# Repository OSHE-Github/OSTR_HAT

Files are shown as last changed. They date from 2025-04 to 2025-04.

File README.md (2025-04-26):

# PCB design for the Open Source Thunniform Robot Project

### Check us out and find more documentation at oshe.io!

### This is the repository for the versitile Raspberry Pi HAT that was developed for the OSTR project in the Open Source Hardware Enterprise at Michigan Tech. This PCB has the following capabilities:
* Can drive two bidirectional 12 V DC motors or four unidirectional 12 V DC motors
* Can control up to two 5 V servos and read from the feedback potentiometer if it's broken out of the servo. These headers can also be used as 5 V ADC inputs
* Has three 3.3 V ADC headers with 3.3 V and GND available. Can be used to read from a potentiometer.
* Two 3.3 V PWM headers with GND and 5 V
* Two GPIO headers with GND and 3.3 V
* Two 3.3 V I2C headers, one is designed/located to be used with the MPU6050 IMU
* Screw terminal 1-wire port designed for a 1-wire based temperature sensor
* Wide input voltage range of 7 V - 30 V using a DFR1015 buck converter
* Capable of monitoring the input voltage. Useful for running off of a battery
* Capable of measuring the output current of both motor drivers (uses two DRV8874 motor drivers)
* Two audio amplifiers designed to be used with custom built piezo electric disk based transducers

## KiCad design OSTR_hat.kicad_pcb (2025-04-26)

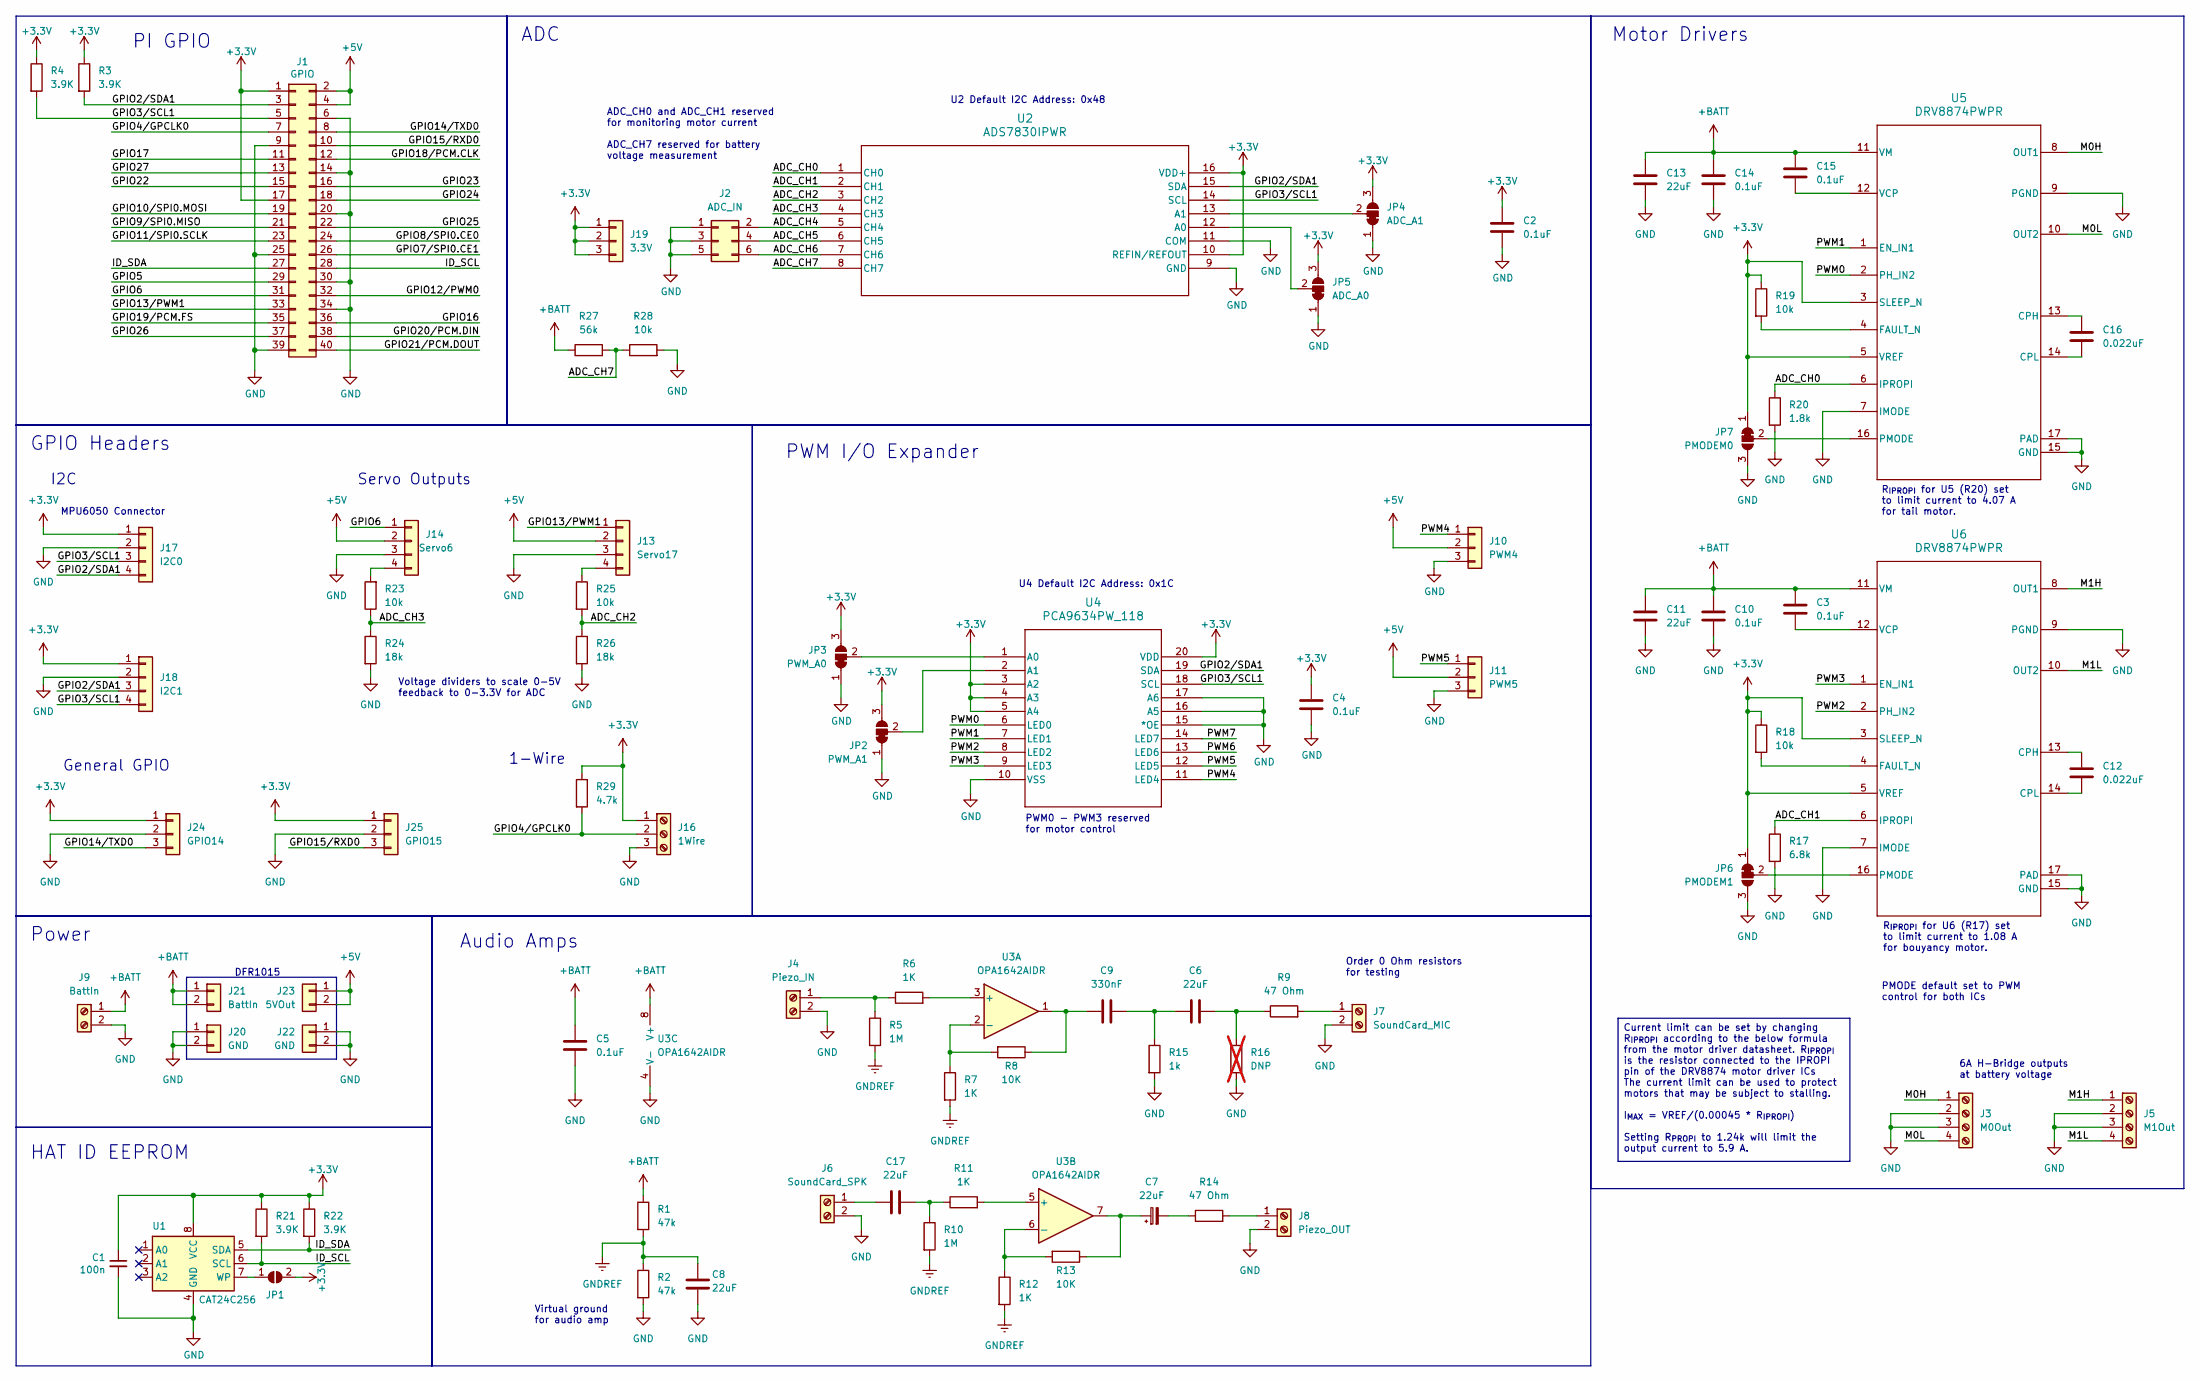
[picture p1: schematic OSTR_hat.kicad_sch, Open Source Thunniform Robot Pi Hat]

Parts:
C1: 100n; C_0603_1608Metric
C2, C4, C5: 0.1uF; C_0603_1608Metric
C3, C15: 0.1uF; C_0603_1608Metric; Part Number C1206C104K5RACTU
C6, C7, C8, C11, C13, C17: 22uF; C_0603_1608Metric
C9: 330nF; C_0603_1608Metric
C10, C14: 0.1uF; C_0603_1608Metric; Part Number GRM155R71C104KA88J
C12, C16: 0.022uF; C_0603_1608Metric; Part Nember C0805C223K5RACTU
J1: GPIO; PinSocket_2x20_P2.54mm_Vertical
J2: ADC_IN; PinHeader_2x03_P2.54mm_Vertical
J3: M0Out; TerminalBlock_Phoenix_MPT-0,5-4-2.54_1x04_P2.54mm_Horizontal
J4: Piezo_IN; TerminalBlock_Phoenix_MPT-0,5-2-2.54_1x02_P2.54mm_Horizontal
J5: M1Out; TerminalBlock_Phoenix_MPT-0,5-4-2.54_1x04_P2.54mm_Horizontal
J6: SoundCard_SPK; TerminalBlock_Phoenix_MPT-0,5-2-2.54_1x02_P2.54mm_Horizontal
J7: SoundCard_MIC; TerminalBlock_Phoenix_MPT-0,5-2-2.54_1x02_P2.54mm_Horizontal
J8: Piezo_OUT; TerminalBlock_Phoenix_MPT-0,5-2-2.54_1x02_P2.54mm_Horizontal
J9: BattIn; TerminalBlock_Phoenix_MKDS-1,5-2-5.08_1x02_P5.08mm_Horizont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
J10: PWM4; PinHeader_1x03_P2.54mm_Vertical
J11: PWM5; PinHeader_1x03_P2.54mm_Vertical
J13: Servo17; PinHeader_1x04_P2.54mm_Vertical
J14: Servo6; PinHeader_1x04_P2.54mm_Vertical
J16: 1Wire; TerminalBlock_Phoenix_MPT-0,5-3-2.54_1x03_P2.54mm_Horizontal
J17: I2C0; PinHeader_1x04_P2.54mm_Vertical
J18: I2C1; PinHeader_1x04_P2.54mm_Vertical
J19: 3.3V; PinHeader_1x03_P2.54mm_Vertical
J20, J22: GND; PinHeader_1x02_P2.54mm_Vertical
J21: BattIn; PinHeader_1x02_P2.54mm_Vertical
J23: 5VOut; PinHeader_1x02_P2.54mm_Vertical
J24: GPIO14; PinHeader_1x03_P2.54mm_Vertical
J25: GPIO15; PinHeader_1x03_P2.54mm_Vertical
JP1: ID_WP; SolderJumper-2_P1.3mm_Open_Pad1.0x1.5mm
JP2: PWM_A1; SolderJumper-3_P1.3mm_Bridged12_Pad1.0x1.5mm
JP3: PWM_A0; SolderJumper-3_P1.3mm_Bridged12_Pad1.0x1.5mm
JP4: ADC_A1; SolderJumper-3_P1.3mm_Bridged12_Pad1.0x1.5mm
JP5: ADC_A0; SolderJumper-3_P1.3mm_Bridged12_Pad1.0x1.5mm
JP6: PMODEM1; SolderJumper-3_P1.3mm_Bridged12_Pad1.0x1.5mm
JP7: PMODEM0; SolderJumper-3_P1.3mm_Bridged12_Pad1.0x1.5mm
R1, R2: 47k; R_0603_1608Metric
R3, R4, R21, R22: 3.9K; R_0603_1608Metric
R5, R10: 1M; R_0603_1608Metric
R6, R7, R11, R12: 1K; R_0603_1608Metric
R8, R13: 10K; R_0603_1608Metric
R9, R14: 47 Ohm; R_0603_1608Metric
R15: 1k; R_0603_1608Metric
R16: DNP; R_0603_1608Metric; not fitted
R17: 6.8k; R_0603_1608Metric
R18, R19, R23, R25, R28: 10k; R_0603_1608Metric
R20: 1.8k; R_0603_1608Metric
R24, R26: 18k; R_0603_1608Metric
R27: 56k; R_0603_1608Metric
R29: 4.7k; R_0603_1608Metric
U1: CAT24C256; SOIC127P600X175-8N
U2: ADS7830IPWR; TSSOP-16_4.4x5mm_P0.65mm
U3: OPA1642AIDR; SOIC-8_3.9x4.9mm_P1.27mm
U4: PCA9634PW_118; TSSOP-20_4.4x6.5mm_P0.65mm
U5, U6: DRV8874PWPR; PWP0016J_M

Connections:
+3.3V: C1.1, C2.1, C4.1, J1.1, J1.17, J16.1, J17.1, J18.1, J19.1, J19.2, J19.3, J24.1, J25.1, JP1.2 (B), JP2.3 (B), JP3.3 (B), JP4.3 (B), JP5.3 (B), JP6.1 (A), JP7.1 (A), R3.1, R4.1, R18.1, R19.1, R21.1, R22.1, R29.1, U1.8 (VCC), U2.10 (REFIN/REFOUT), U2.16 (VDD+), U4.3 (A2), U4.4 (A3), U4.5 (A4), U4.20 (VDD), U5.3 (SLEEP_N), U5.5 (VREF), U6.3 (SLEEP_N), U6.5 (VREF)
+5V: J1.2, J1.4, J10.2, J11.2, J13.2, J14.2, J23.1, J23.2
+BATT: C3.1, C5.1, C10.1, C11.1, C13.1, C14.1, C15.1, J9.1, J21.1, J21.2, R1.1, R27.1, U3.8 (V+), U5.11 (VM), U6.11 (VM)
/ADC_CH0: R20.1, U2.1 (CH0), U5.6 (IPROPI)
/ADC_CH1: R17.1, U2.2 (CH1), U6.6 (IPROPI)
/ADC_CH2: R25.2, R26.1, U2.3 (CH2)
/ADC_CH3: R23.1, R24.1, U2.4 (CH3)
/ADC_CH4: J2.2, U2.5 (CH4)
/ADC_CH5: J2.4, U2.6 (CH5)
/ADC_CH6: J2.6, U2.7 (CH6)
/ADC_CH7: R27.2, R28.1, U2.8 (CH7)
/GPIO2/SDA1: J1.3, J17.4, J18.3, R3.2, U2.15 (SDA), U4.19 (SDA)
/GPIO3/SCL1: J1.5, J17.3, J18.4, R4.2, U2.14 (SCL), U4.18 (SCL)
/GPIO4/GPCLK0: J1.7, J16.2, R29.2
/GPIO5: J1.29
/GPIO6: J1.31, J14.1
/GPIO7/SPI0.CE1: J1.26
/GPIO8/SPI0.CE0: J1.24
/GPIO9/SPI0.MISO: J1.21
/GPIO10/SPI0.MOSI: J1.19
/GPIO11/SPI0.SCLK: J1.23
/GPIO12/PWM0: J1.32
/GPIO13/PWM1: J1.33, J13.1
/GPIO14/TXD0: J1.8, J24.3
/GPIO15/RXD0: J1.10, J25.3
/GPIO16: J1.36
/GPIO17: J1.11
/GPIO18/PCM.CLK: J1.12
/GPIO19/PCM.FS: J1.35
/GPIO20/PCM.DIN: J1.38
/GPIO21/PCM.DOUT: J1.40
/GPIO22: J1.15
/GPIO23: J1.16
/GPIO24: J1.18
/GPIO25: J1.22
/GPIO26: J1.37
/GPIO27: J1.13
/ID_SCL: J1.28, R21.2, U1.6 (SCL)
/ID_SDA: J1.27, R22.2, U1.5 (SDA)
/M0H: J3.1, U5.8 (OUT1)
/M0L: J3.4, U5.10 (OUT2)
/M1H: J5.1, U6.8 (OUT1)
/M1L: J5.4, U6.10 (OUT2)
/PWM0: U4.6 (LED0), U5.2 (PH_IN2)
/PWM1: U4.7 (LED1), U5.1 (EN_IN1)
/PWM2: U4.8 (LED2), U6.2 (PH_IN2)
/PWM3: U4.9 (LED3), U6.1 (EN_IN1)
/PWM4: J10.1, U4.11 (LED4)
/PWM5: J11.1, U4.12 (LED5)
/PWM6: U4.13 (LED6)
/PWM7: U4.14 (LED7)
GND: C1.2, C2.2, C4.2, C5.2, C8.2, C10.2, C11.2, C13.2, C14.2, J1.6, J1.9, J1.14, J1.20, J1.25, J1.30, J1.34, J1.39, J2.1, J2.3, J2.5, J3.2, J3.3, J4.2, J5.2, J5.3, J6.2, J7.2, J8.2, J9.2, J10.3, J11.3, J13.3, J14.3, J16.3, J17.2, J18.2, J20.1, J20.2, J22.1, J22.2, J24.2, J25.2, JP2.1 (A), JP3.1 (A), JP4.1 (A), JP5.1 (A), JP6.3 (B), JP7.3 (B), R2.2, R15.2, R16.2, R17.2, R20.2, R24.2, R26.2, R28.2, U1.4 (GND), U2.9 (GND), U2.11 (COM), U3.4 (V-), U4.10 (VSS), U4.15 (*OE), U4.16 (A5), U4.17 (A6), U5.7 (IMODE), U5.9 (PGND), U5.15 (GND), U5.17 (PAD), U6.7 (IMODE), U6.9 (PGND), U6.15 (GND), U6.17 (PAD)
GNDREF: C8.1, R1.2, R2.1, R5.2, R7.2, R10.2, R12.2
unnamed: C6.1, C9.2, R15.1
unnamed: C6.2, R9.1, R16.1
unnamed: C7.1, R13.1, U3.7
unnamed: C7.2, R14.1
unnamed: C9.1, R8.1, U3.1
unnamed: C17.2, R10.1, R11.1
unnamed: J4.1, R5.1, R6.1
unnamed: C17.1, J6.1
unnamed: J7.1, R9.2
unnamed: J8.1, R14.2
unnamed: J13.4, R25.1
unnamed: J14.4, R23.2
unnamed: JP1.1 (A), U1.7 (WP)
unnamed: JP2.2 (C), U4.2 (A1)
unnamed: JP3.2 (C), U4.1 (A0)
unnamed: JP4.2 (C), U2.13 (A1)
unnamed: JP5.2 (C), U2.12 (A0)
unnamed: JP6.2 (C), U6.16 (PMODE)
unnamed: JP7.2 (C), U5.16 (PMODE)
unnamed: R6.2, U3.3 (+)
unnamed: R7.1, R8.2, U3.2 (-)
unnamed: R11.2, U3.5 (+)
unnamed: R12.1, R13.2, U3.6 (-)
unnamed: C16.1, U5.13 (CPH)
unnamed: C16.2, U5.14 (CPL)
unnamed: R19.2, U5.4 (FAULT_N)
unnamed: C15.2, U5.12 (VCP)
unnamed: C12.1, U6.13 (CPH)
unnamed: C12.2, U6.14 (CPL)
unnamed: R18.2, U6.4 (FAULT_N)
unnamed: C3.2, U6.12 (VCP)

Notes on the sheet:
U2 Default I2C Address: 0x48
PWM I/O Expander
HAT ID EEPROM
1-Wire
GPIO Headers
MPU6050 Connector
I2C
PMODE default set to PWM control for both ICs
Motor Drivers
DFR1015
PI GPIO
U4 Default I2C Address: 0x1C
Order 0 Ohm resistors for testing
Voltage dividers to scale 0-5V feedback to 0-3.3V for ADC
R_{IPROPI} for U6 (R17) set to limit current to 1.08 A for bouyancy motor.
Power
6A H-Bridge outputs at battery voltage
ADC
General GPIO
R_{IPROPI} for U5 (R20) set to limit current to 4.07 A for tail motor.
Virtual ground for audio amp
Audio Amps
ADC_CH0 and ADC_CH1 reserved for monitoring motor current ADC_CH7 reserved for battery voltage measurement
PWM0 - PWM3 reserved for motor control
Servo Outputs
Current limit can be set by changing R_{IPROPI} according to the below formula from the motor driver datasheet. R_{IPROPI} is the resistor connected to the IPROPI pin of the DRV8874 motor driver ICs The current limit can be used to protect motors that may be subject to stalling. I_{MAX} = VREF/(0.0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

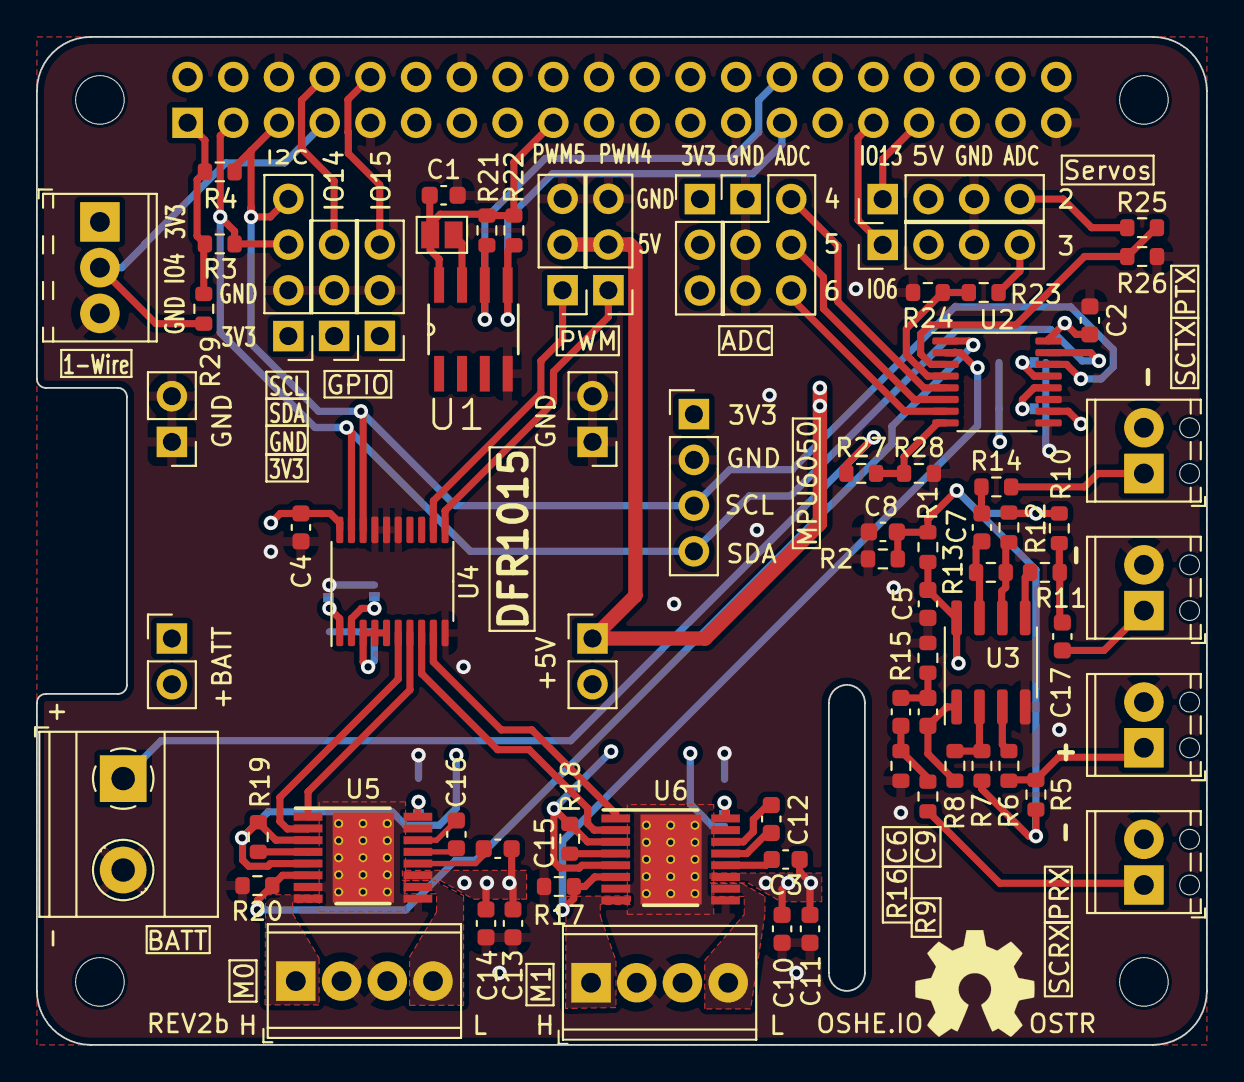
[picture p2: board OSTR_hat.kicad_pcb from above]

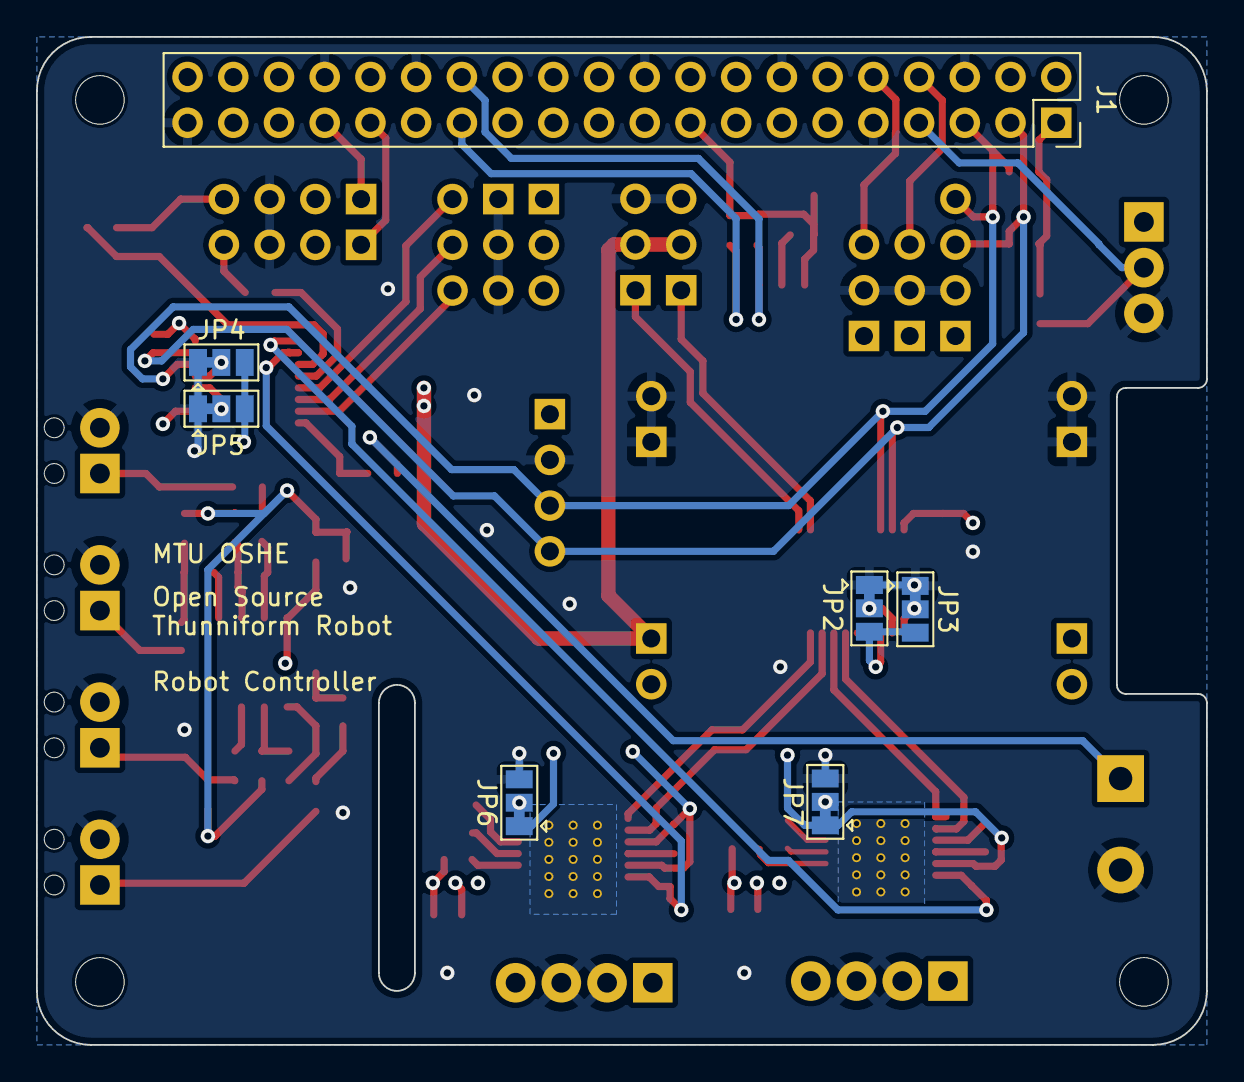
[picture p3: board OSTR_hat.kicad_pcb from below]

Board: 4 copper layers, 65.0 x 56.0 mm, 86 parts (7 on the bottom side), 63 nets.

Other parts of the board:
MH1, MH2, MH3, MH4: MountingHole_2.7mm_M2.5

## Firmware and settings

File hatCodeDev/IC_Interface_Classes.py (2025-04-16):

#from w1thermsensor import W1ThermSensor, Unit

from smbus2 import SMBus
import time

# use mpu6050 library for IMU. Documentation for that library has good example code

# for servos use: from gpiozero import Servo

## Temp sensor
# Run "sudo dtoverlay w1-gpio gpiopin=4" to enable 1-wire


## IMU

ADDRIMU = 0x68
freq_divider = 0x04
g = 9.8 # gravity acceleration (m/s^2)


## ADC

# ADC I2C Address
ADDRADC = 0x48

# ADC pins
MD0I = 0    # Motor 0 current
MD1I = 1    # Motor 1 current
SADC2 = 2   # Servo feedback
SADC3 = 3   # servo feedback
VBATT = 7   # Battery voltage, scaled to 0-3.3V

# Command Byte
SEINPUTS = 0x80     # Differential inputs
DEINPUTS = 0x00     # Single-ended inputs
CSSHIFT = 4         # shift to apply to desired pin
PDMODE = 0x04       # power-down mode (Internal Reference OFF and A/D Converter ON)

# Single-Ended PIN Look Up Table -- to convert ADC pin to ADC channel
SEPINLUT = [0x8, 0xC, 0x9, 0xD, 0xA, 0xE, 0xB, 0xF]

# ADC Conversion Constants
ADCREF = 3.3

# Motor current monitoring
AIPROPI = 0.000450      # motor driver current monitor current gain
# ADC count to motor current (A)
ADCM0OI = (ADCREF / 255) / (1800 * AIPROPI)     #Motor 0, 1.8k RPROPI for 4.07 A limit
ADCM1OI = (ADCREF / 255) / (6800 * AIPROPI)     #Motor 1, 6.8k RPROPI for 1.08 A limit


# Battery voltage monitoring
RBATL = 10000
RBATU = 56000
# ADC count to battery voltage (V)
ADCBATTC = (RBATL + RBATU)/RBATL * (ADCREF/255)


## PWM

# PWM chip I2C Address
ADDRPWM = 0x1C

# Define various registers
MODE1 = 0x00
MODE2 = 0x01
PWM0 = 0x02
LEDOUT0 = 0x0C  # pins 0-3
LEDOUT1 = 0x0D  # pins 4-7

# Define control bytes
CTRL = 0x00
CTRLAI = 0x80   # Autoincrement flag


## Motor Drivers

# Driver 0 PWM pins
M0P1 = 1
M0P2 = 0

# Driver 1 PWM pins
M1P1 = 3
M1P2 = 2

# Motor driver modes
MDMRC = 0       # Reverse, Coast -- doesn't seem to make motor move
MDMFC = 1       # Forward, Coast -- doesn't seem to make motor move
MDMFB = 2       # Forward, Brake
MDMRB = 3       # Reverse, Brake

#defaut delay
DEFDELAY = 0.1


## ADC

class ADC:
    def __init__(self, addr, i2cbus):
        self.addr = addr        # I2C address of chip
        self.i2cbus = i2cbus
    
    def read(self, pin):
        #print("ADC read")
        #print(f"Control byte: {(SEPINLUT[pin] << CSSHIFT) | PDMODE}")
        self.i2cbus.write_byte(self.addr, (SEPINLUT[pin] << CSSHIFT) | PDMODE)  # Initiate a read on pin
        time.sleep(DEFDELAY)
        return self.i2cbus.read_byte(self.addr)                                  # Get ADC reading and return it


## PWM Generator

class PWMExpander:
    def __init__(self, addr, i2cbus):
        self.addr = addr        # I2C address of chip
        self.i2cbus = i2cbus
        #control byte: 1000 0000 0x80
        # MODE1 register: 1000 0000 0x80
        # MODE2 register: 0000 0101 0x05
        #print(f"MODE: {self.i2cbus.read_i2c_block_data(self.addr, CTRLAI, 18)}")
        #print(f"MODE1: {self.i2cbus.read_i2c_block_data(self.addr, 0, 1)}")
        #print(f"MODE2: {self.i2cbus.read_i2c_block_data(self.addr, 1, 1)}")
        self.i2cbus.write_i2c_block_data(self.addr, CTRLAI, [0x00, 0x1D])
        time.sleep(DEFDELAY)
        #print(f"MODE: {self.i2cbus.read_i2c_block_data(self.addr, CTRLAI, 18)}")
        
    # set PWM duty cycle and set pin mode to PWM
    # pin: 0x00-0x07
    # duty: 0-256
    def setPWM(self, pin, duty):
        #print("PWM setPWM")
        #self.setPINMODE(pin, 0)                                     # turn pin off
        #print(f"Control byte: {PWM0 + pin}, Duty: {duty}")
        duty = 256-duty
        if (duty > 256 or duty < 0):
            print("duty out of range")
            return 1
        self.i2cbus.write_byte_data(self.addr, PWM0 + pin, duty)    # write duty to pin PWM register
        time.sleep(DEFDELAY)
        #print(f"MODE: {self.i2cbus.read_i2c_block_data(self.addr, CTRLAI, 18)}")
        self.setPINMODE(pin, 2)                                     # enable PWM on pin
        
    
    # set pin output mode
    # 0 - on; 1 - off; 2 - PWM
    def setPINMODE(self, pin, mode):
        #print("PWM setPINMODE")
        pinStates = self.i2cbus.read_i2c_block_data(self.addr, CTRLAI | (LEDOUT0),2)      # get current state
        #print(f"Control Byte: {CTRLAI | (LEDOUT0 + int(pin/4))}")
        #print(f"Current pinStates: {pinStates}")
        pinStates[int(pin/4)] = pinStates[int(pin/4)] & (0xFF^(0x3 << 2*(pin%4)))   # clear bits associated with given pin
        pinStates[int(pin/4)] = pinStates[int(pin/4)] | (mode << 2*(pin%4))         # set bits associated with given pin to mode
            
        #print(f"New pinStates: {pinStates}")
        self.i2cbus.write_i2c_block_data(self.addr, CTRLAI | (LEDOUT0), pinStates)      # set new state
        time.sleep(DEFDELAY)
        #print(f"MODE: {self.i2cbus.read_i2c_block_data(self.addr, CTRLAI, 18)}")
        

## Motor Drivers

class motorDriver:
    # pwmexpander - PWMExpander object that controls the IO expander
    # pin1 - PWMExpander pin connected to EN_IN1 pin
    # pin2 = PWMExpander pin connected to PH_IN2 pin
    def __init__(self, pwmexpander, pin1, pin2):
        self.pin = [0,0]
        self.pin[0] = pin1
        self.pin[1] = pin2
        self.pwmexpander = pwmexpander
        
    # mode - left = constant pin state; right = constant pin
    # 0 - 00 - coast; reverse
    # 1 - 01 - coast; forward
    # 2 - 10 - brake; forward
    # 3 - 11 - brake; reverse
    # duty = 0-256, 0 = stop, 256 = full speed
    def go(self, mode, duty):
        #print("Motor go")
        #print(f"Pin: {self.pin[mode%2]}, Mode: {int(mode/2)}")
        self.pwmexpander.setPINMODE(self.pin[mode%2], int(mode/2))     # set value of constant pin
        
        if duty == 0:
            #print(f"Pin: {self.pin[1-mode%2]}, Mode: 1")
            self.pwmexpander.setPINMODE(self.pin[1-mode%2], 1)
            
        else:
            #print(f"Pin: {self.pin[1-mode%2]}, Duty: {duty}")
            self.pwmexpander.setPWM(self.pin[1-mode%2], duty)
            
    
    # mode - 0 = coast; 1 = brake
    def stop(self, mode):
        #print("Motor stop")
        self.pwmexpander.setPINMODE(self.pin[0], mode)
        self.pwmexpander.setPINMODE(self.pin[1], mode)
        
# Example code:

# Initialize everything
i2cbus = SMBus(1)
print("\nADC init")
adc = ADC(ADDRADC, i2cbus)
print("\npwmexpander init")
pwmexpander = PWMExpander(ADDRPWM, i2cbus)
print("\nmotor0 init")
motor0 = motorDriver(pwmexpander, M0P1, M0P2)
print("\nmotor1 init")
motor1 = motorDriver(pwmexpander, M1P1, M1P2)

    
# Check battery voltage and motor currents

# Start motor 0 at given duty (0-256)
speed = int(input("M0: "))
motor0.go(MDMFB, speed)
speed = int(input("M1: "))
motor1.go(MDMFB, speed)
# stop motor 0 with given stop mode
stopmode = int(input("Stop Mode: "))
motor0.stop(stopmode)
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

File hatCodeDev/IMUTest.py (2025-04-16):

from mpu6050 import MPU6050

i2c_bus = 1
device_address = 0x68
freq_divider = 0x04

# Make an MPU6050
mpu = MPU6050(i2c_bus, device_address, freq_divider)

# Initiate your DMP
mpu.dmp_initialize()
mpu.set_DMP_enabled(True)

packet_size = mpu.DMP_get_FIFO_packet_size()
FIFO_buffer = [0]*64

while True: # infinite loop
    if mpu.isreadyFIFO(packet_size): # Check if FIFO data are ready to use...
                
        FIFO_buffer = mpu.get_FIFO_bytes(packet_size) # get all the DMP data here
                        
        q = mpu.DMP_get_quaternion_int16(FIFO_buffer)
        grav = mpu.DMP_get_gravity(q)
        roll_pitch_yaw = mpu.DMP_get_euler_roll_pitch_yaw(q)
                
        print('roll: ' + str(roll_pitch_yaw.x))
        print('pitch: ' + str(roll_pitch_yaw.y))
        print('yaw: ' + str(roll_pitch_yaw.z))
        print('\n')

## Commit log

2025-04-16 removed imports for IMU, servos, and temp sensor. Added comments for recommended libraries for them
2025-04-17 Generated new gerbers
2025-04-26 Added stackup and description to PCB design
    [OSTR_hat.kicad_pcb]
2025-04-26 Updated rev2b gerbers
    [OSTR_hat-B_Cu.gbl, OSTR_hat-B_Mask.gbs, OSTR_hat-B_Silkscreen.gbo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]
